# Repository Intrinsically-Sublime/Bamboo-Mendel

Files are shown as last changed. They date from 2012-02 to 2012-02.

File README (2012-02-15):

---Description---

The idea

Make RepRap more accessible to those without 3D printing technology already

Goals

1) Minimal unique piece count to allow for production from molds.

2) Parts available world wide.

3) Modular for multiple configurations.

Outcome

1) Only eight unique pieces.

2)a Frame made can be made from: Bamboo, Conduit, tubing, pipe, ...
b Tapered holes for Z axis guides for metric or imperial materials.
c No critical bolt sizes.
d Uses (wire rope / aircraft cable / fishing wire) instead of belts.

3) see pictures and continue reading.

Color code for renderings

Yellow = Bamboo/conduit/tubing/etc.
White = Printed or molded parts.
Black = Metal parts.
Red = Aircraft cable/fishing wire/wire rope
Green = Sheet material. (plywood/plexiglass/...)

Additional benefits

A) If printed from PLA and made from bamboo most of it can be composted.

B) You can grow the frame in most habitable parts of the world.

C) Can be built larger scale for producing furniture and larger items using a frostruder and earth based pastes.

D) As Twotimes pointed out if you use thingiverse.com/thing:4439 it will be almost entirely printable

Attribution
Modeled using Spacexulas Nema 17 thingiverse.com/thing:3940
Uses Herringbone gears from Rhys-Jones thingiverse.com/thing:5111
Drums derived from 2ROBOTGUYs pulley thingiverse.com/thing:5109
Motor mounts derived from Wades extruder thingiverse.com/thing:1794
Requires PrusaJr style bushings
thingiverse.com/thing:4177 or
thingiverse.com/thing:4501 or
thingiverse.com/thing:4434 or
thingiverse.com/thing:4460

Updates

Dec 27/10 Added Vertex_2.stl Easier to scale and make molds of.
thingiverse.com/thing:5318

Dec 27/10 The original files were scaled wrong and needed to be scaled by 1.333. All the files have been replaced. 

---Instructions---

I will add instruction at some point but for now just a little on how it should work.

All axis are geared down using herringbone gears for high torque to overcome friction. Currently using Rhys-Jones Herringbones gears from thing thingiverse.com/thing:5111

The Aircraft cable is wrapped around the Z axis axle for maximum torque and highest resolution. While it is wrapped around drums on the X and Y axis for higher speeds while still being geared down for torque. I believe two to three wraps around the axle and/or drum should provide adequate gripe as long as the springs used to keep the tension are very strong.

It currently uses prusa style bushing for the guides.
For longer lasting bushings use thingiverse.com/thing:4501 with bronze bushings in them similar to these princessauto.com/components/com_virtuemart/shop_image/product/3872025.jpg

The vertexes. (should be made parameterized)
They are currently modeled for 20mm id bamboo. They have a tapered hole for the Z axis rod which will allow for slight scaling without any issues. The holes for the axles are 8.5mm and will require modifying/drilling if scaled much. They are designed to expand inside of the hollow material when a screw or lag bolt is screwed in.

I am aware this will be a little hard to assemble square and true due to the lack of adjustment, but possible. It will require shims etc.

Hopefully everything works as designed but even if it doesn't maybe it will inspire others.

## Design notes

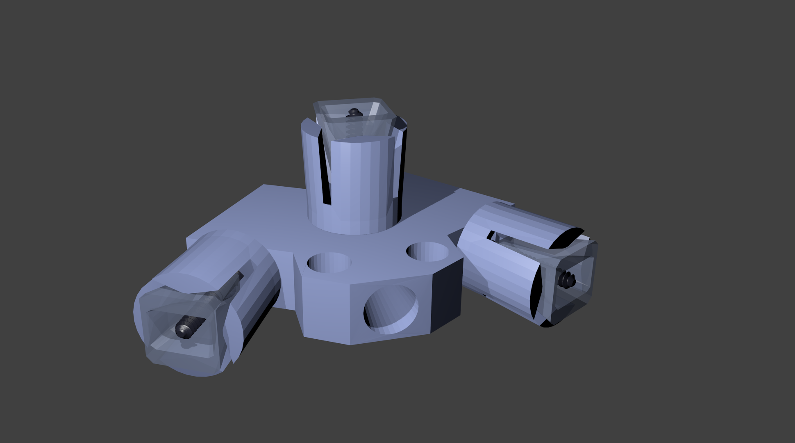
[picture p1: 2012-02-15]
Universal_Vertex_Screw.png

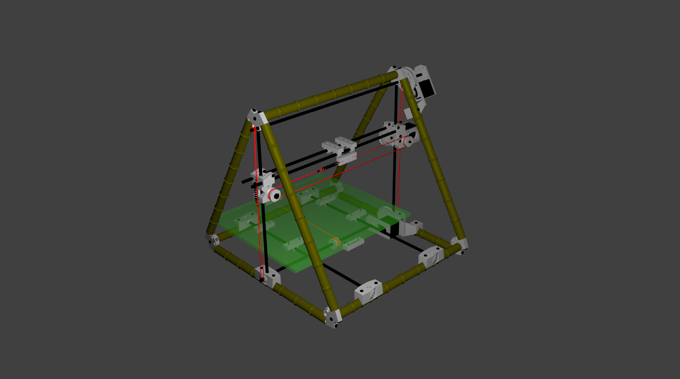
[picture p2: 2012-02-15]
Bamboo Mendel2.png

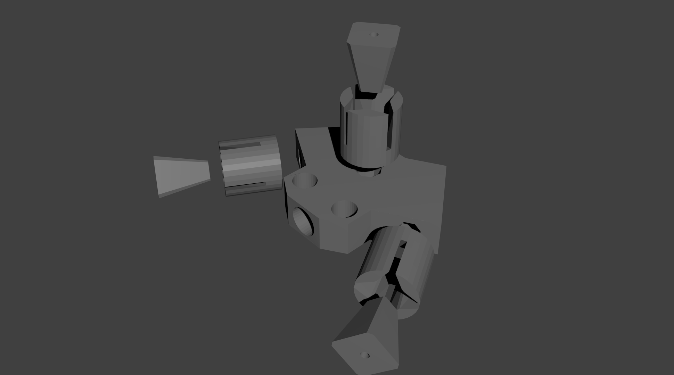
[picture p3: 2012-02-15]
Vertex_2.png

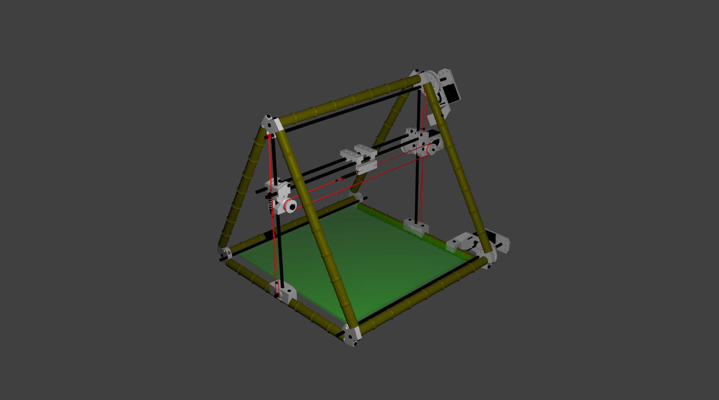
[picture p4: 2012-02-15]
Bamboo Mendel4.png

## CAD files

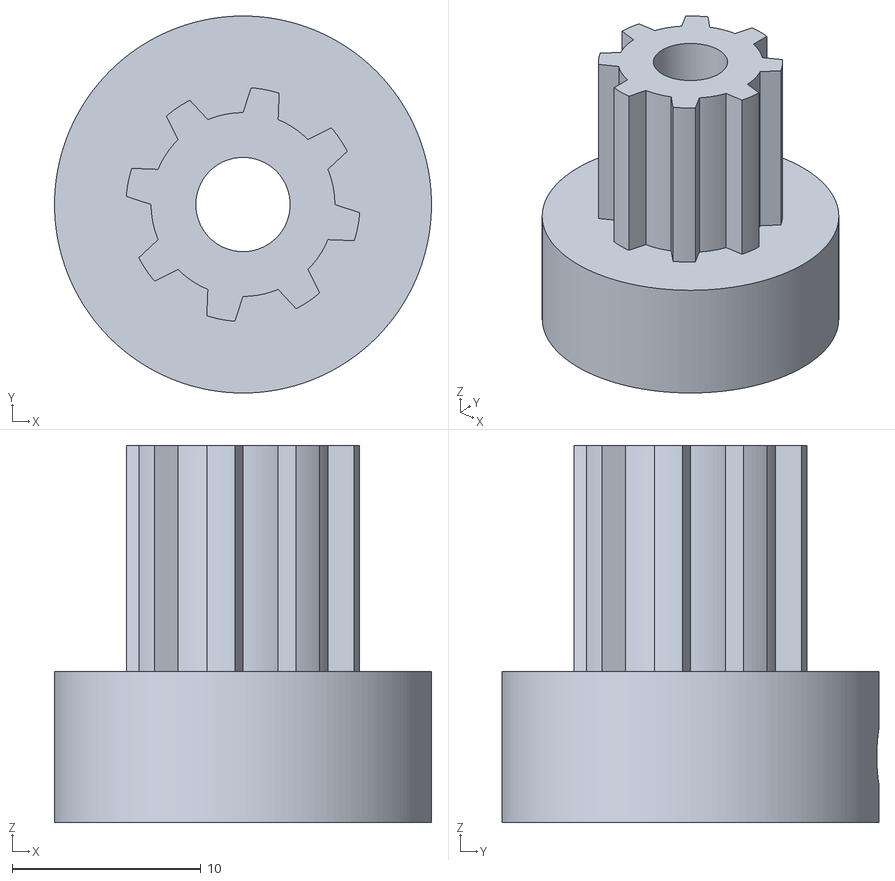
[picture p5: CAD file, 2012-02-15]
FULLER_LOCK_PULLEY_OVERSIZED.STL
20.0 x 20.0 x 20.0

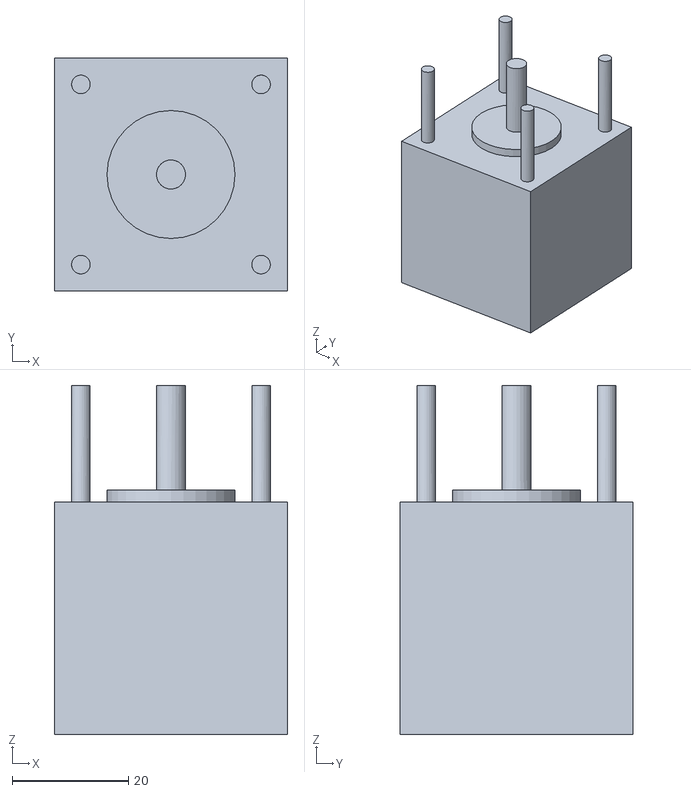
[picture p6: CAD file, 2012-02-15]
nema17fuse.stl
40.1 x 40.1 x 60.0

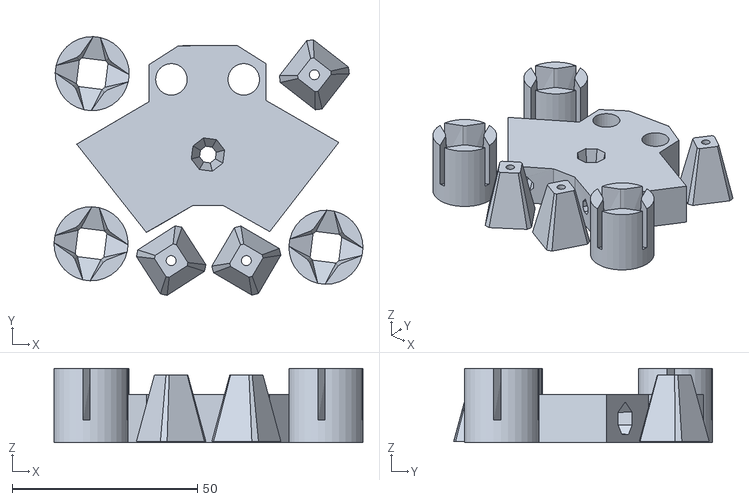
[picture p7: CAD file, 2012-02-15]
STL's/vertex_2.stl
83.4 x 69.8 x 20.1

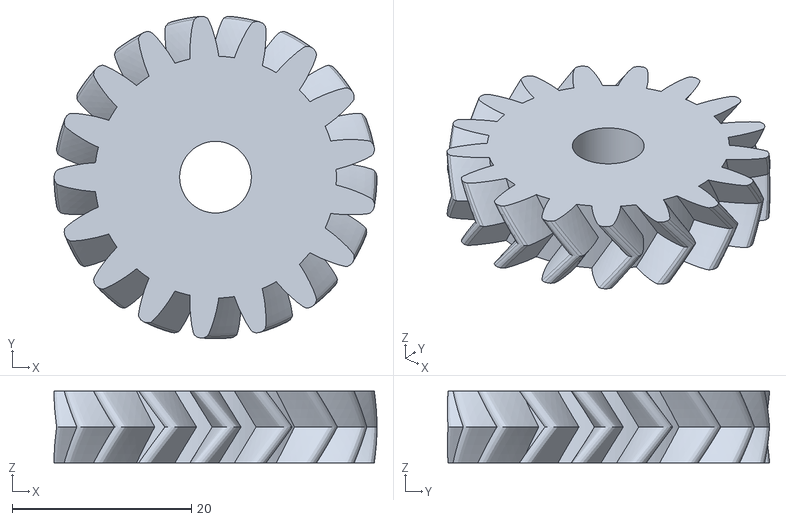
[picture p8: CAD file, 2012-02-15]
extgearL.stl
36.1 x 36.0 x 8.00

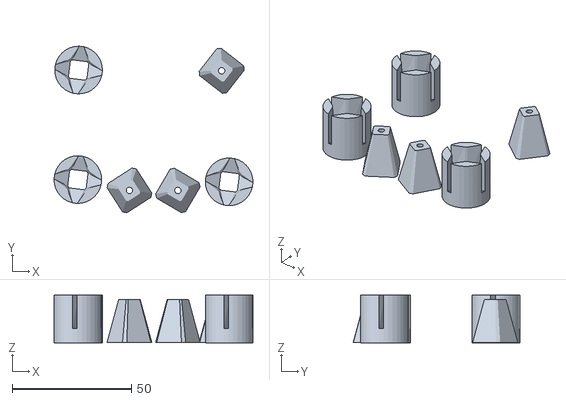
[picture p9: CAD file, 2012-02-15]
STL's/vertex_2_inserts.stl
83.4 x 69.8 x 20.0

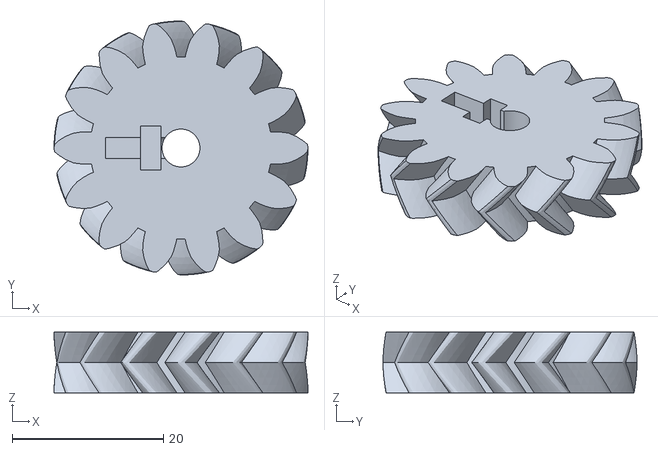
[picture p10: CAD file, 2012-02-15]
extgearS.stl
33.5 x 33.5 x 8.00

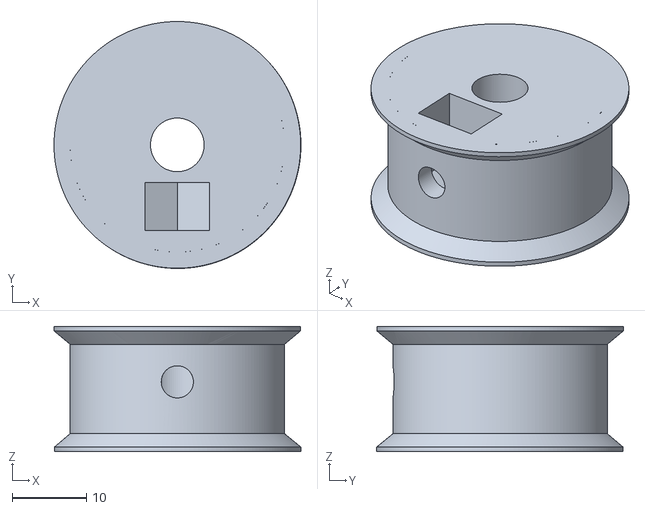
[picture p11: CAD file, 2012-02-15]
STL's/large_drum.stl
33.2 x 33.1 x 16.8

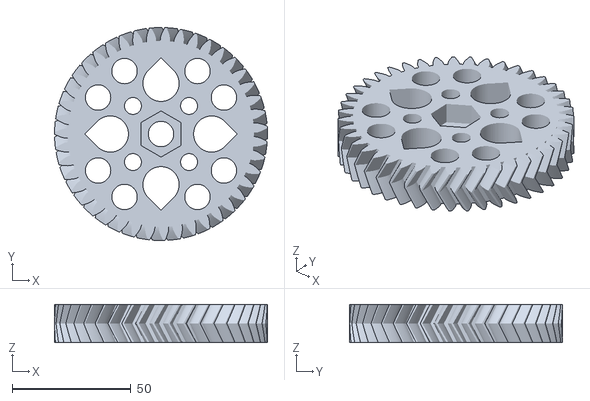
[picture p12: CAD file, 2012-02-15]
STL's/DrivenGear.stl
89.5 x 89.5 x 16.0

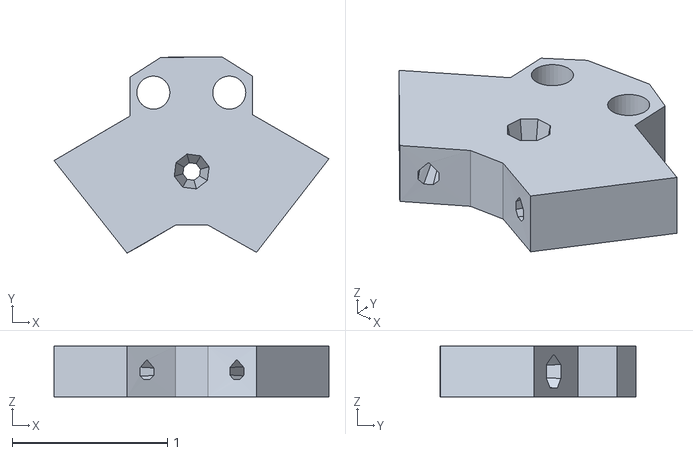
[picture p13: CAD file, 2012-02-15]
Temp.stl
1.77 x 1.26 x 0.325

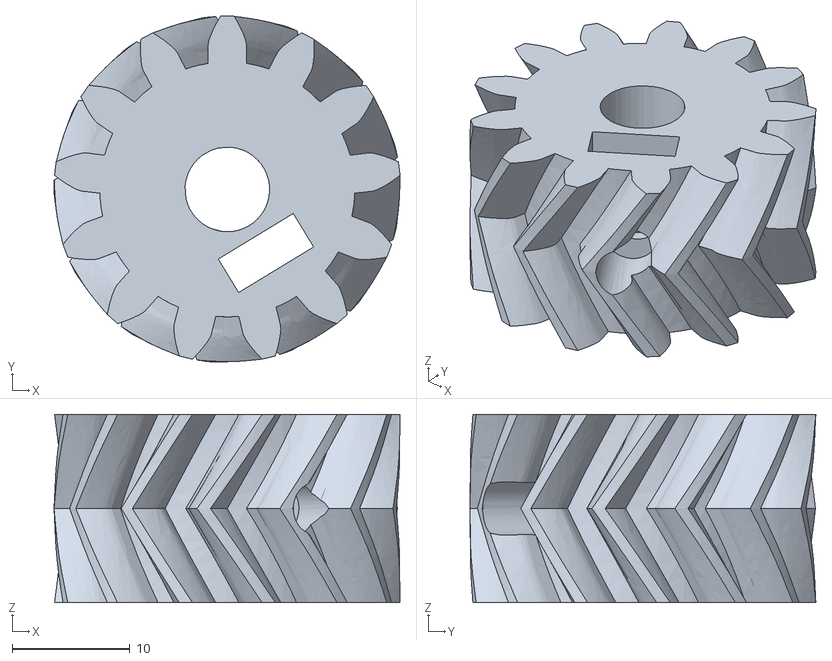
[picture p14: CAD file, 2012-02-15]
STL's/DriveGear.stl
29.4 x 29.4 x 16.0

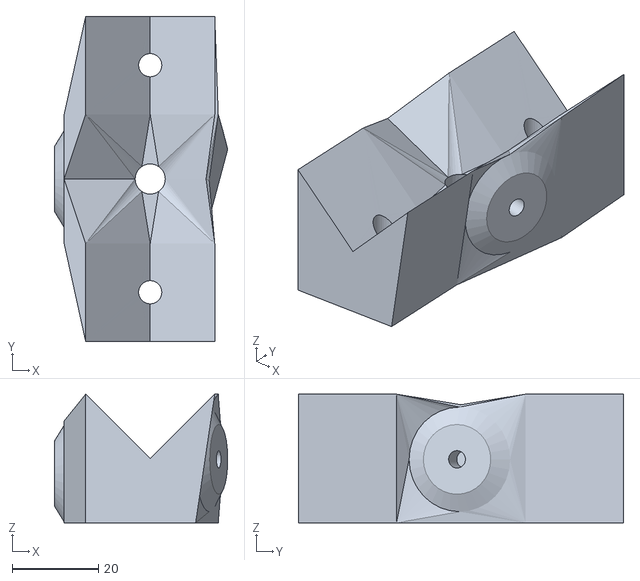
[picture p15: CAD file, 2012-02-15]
STL's/large_block.stl
40.3 x 75.5 x 29.9

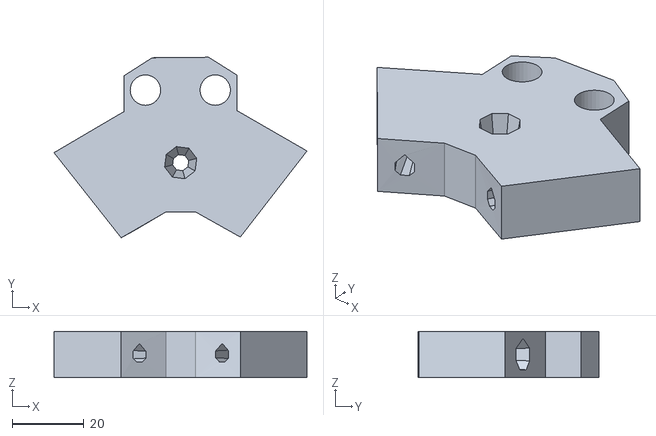
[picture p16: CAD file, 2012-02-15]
STL's/vertex_2_body.stl
70.7 x 50.5 x 13.0

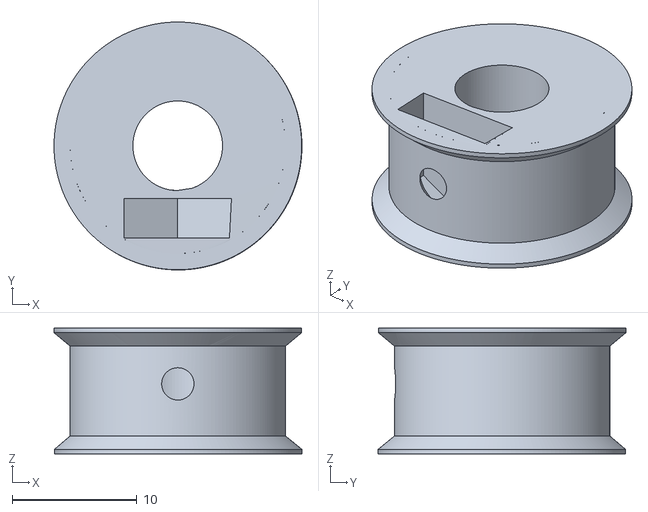
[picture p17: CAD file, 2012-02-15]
STL's/small_drum.stl
19.9 x 19.9 x 10.1

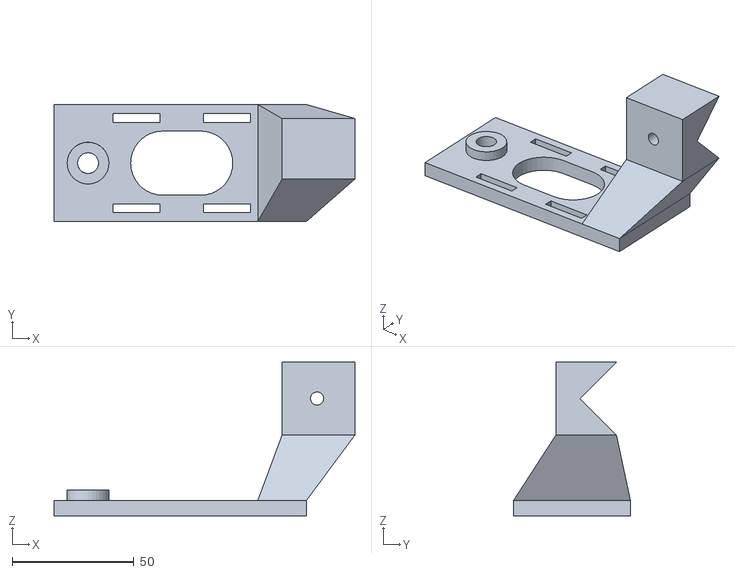
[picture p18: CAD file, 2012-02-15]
STL's/motor_A.stl
123.8 x 48.1 x 63.3

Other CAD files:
STL's/z_stage.stl
STL's/vertex.stl
STL's/small_block.stl
STL's/motor_B.stl
Bamboo_Mendel_sheet.blend
Universal_Vertex_Screw.blend
Vertex_2.1.blend
Vertex_2.blend
